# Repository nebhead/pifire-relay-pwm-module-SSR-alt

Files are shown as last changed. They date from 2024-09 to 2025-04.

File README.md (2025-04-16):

# PiFire Solid State Relay (SSR) Module PCB ALT (v1.0.0-alt) KiCad Files

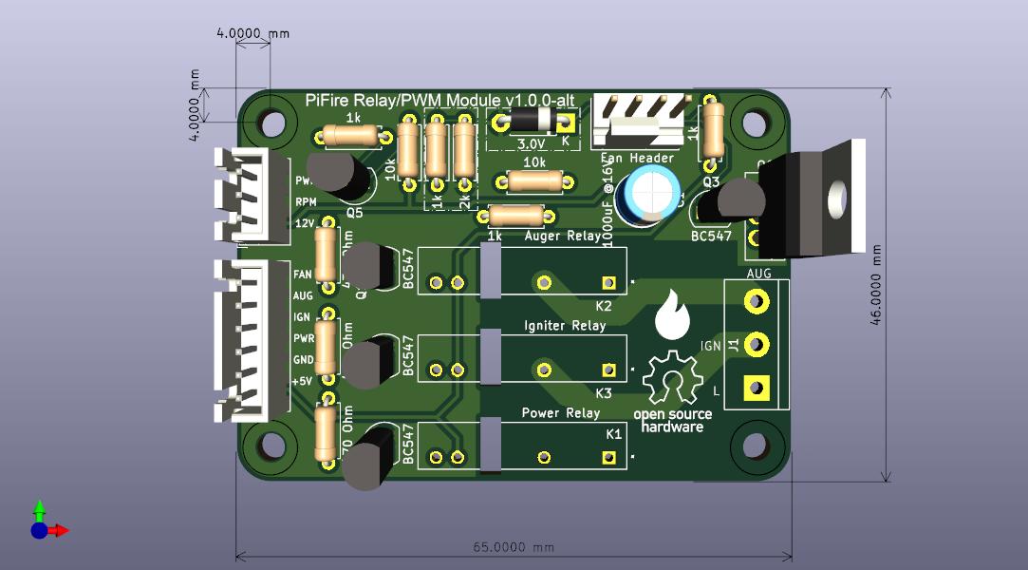
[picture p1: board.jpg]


## What is this? 

This PCB is designed to support SSR relays for controlling incoming Power(L) to the Igniter and Auger.  This board also has circuitry to support a 12V PWM fan.  This board uses compact solid state relays that are able to handle high power. This is an alternative to using an off the shelf relay module which simplifies the wiring and even allows you to use the OEM harness.

This version of the board was designed with help from user @labmonkeyrat on Discord. PCB mounted fuses have been removed, preferring inline fuses external to the board. The fan power is controlled from the high side (12V) instead of ground (original design).  

The design intent for this board was to make a DIY accessible PCB that can be more easily put together by the maker/enthusiast of almost any skill level.  Full size components are used in most cases and most (if not all) parts should be readily available to order online.  See the [Interactive BOM](#interactive-bom) for more details about the parts used and links to order.

### Important Notes

This PCB is intended to be used with the 4.0.x PCB design ([linked below](#links-to-the-pcbs-in-this-family-of-pifire-boards)) in conjunction with v1.8.x or later of the PiFire software.

The G3MB Relay footprints have been left out of this release because they were sourced from SnapMagic (for free), but are not licensed for re-distribution.  If you plan to edit this board, you may need to source those files from SnapMagic directly and add them to this project in the G3MB folder.

### What is PiFire? 

PiFire is a SBC based Pellet Smoker Controller.  More details can be found [here](https://nebhead.github.io/PiFire) or [at the GitHub repo](https://github.com/nebhead/pifire). 

## What's in this Repository?

### KiCad Project Files 
In this repository you will find the latest KiCad design files for the  PCB.  Simply load the project file (.kicad_pro) into the KiCad software and you should be able to edit as needed.  Or if you just want to get this board made, jump to the production section below.

### Interactive BOM

There is an interactive BOM located in the [/bom](bom/) folder which details the parts and provides some pin information as well.  Use this to gather the components you may need to build this board out and refer back to it for placement help.    

[BOM + Pin Info](https://nebhead.github.io/pifire-relay-pwm-module-SSR-alt)

_This is a standalone HTML file that was autogenerated by the excellent plugin for KiCad. See the plugin here: [https://github.com/openscopeproject/InteractiveHtmlBom](https://github.com/openscopeproject/InteractiveHtmlBom)_

### PDF of the Schematic

Preview the schematic in PDF format here: [Schematic](schematic.pdf)

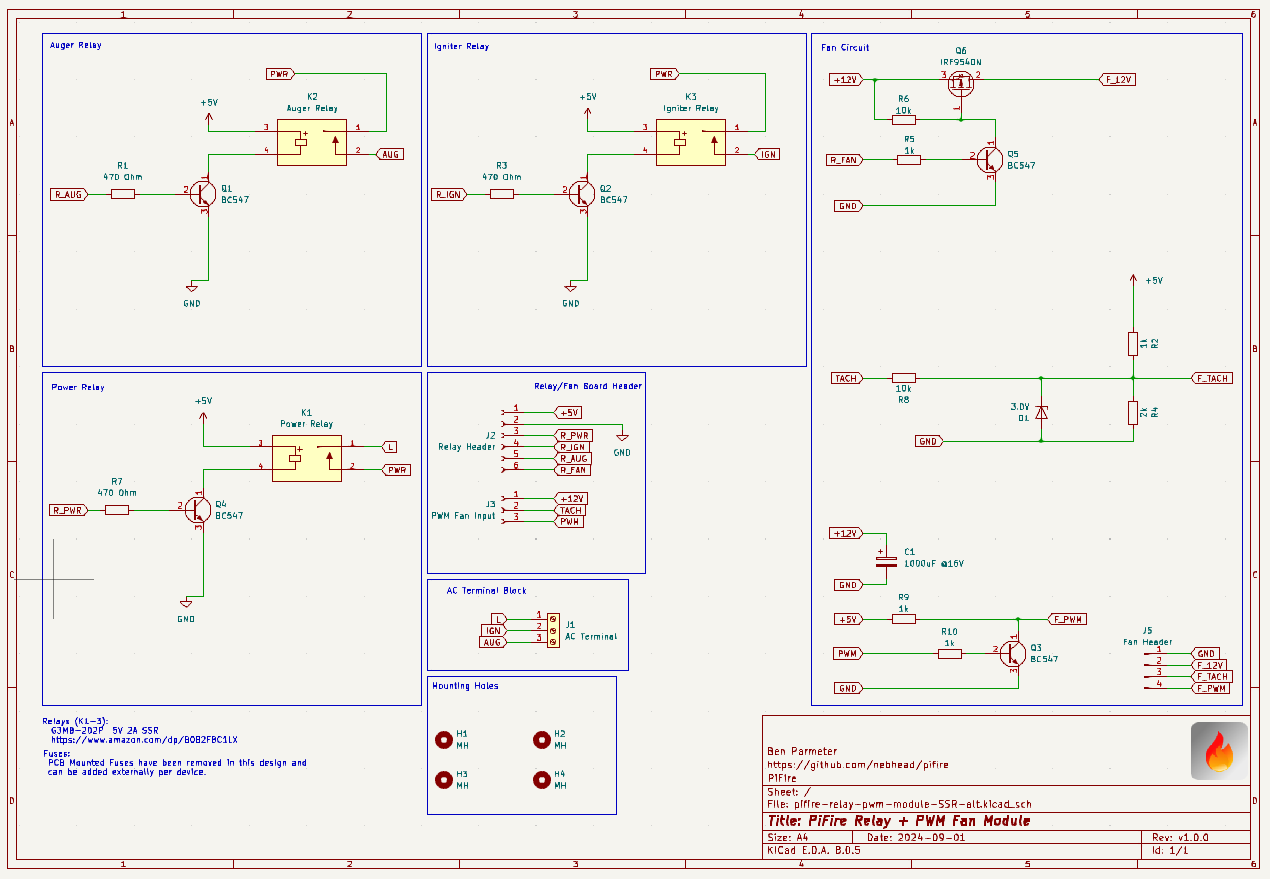
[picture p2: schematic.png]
Schematic PNG


### PWM Fan Pinout

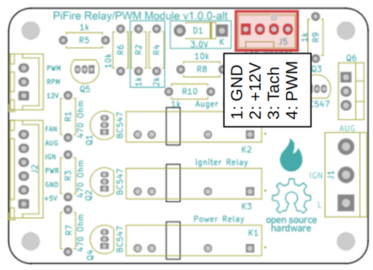
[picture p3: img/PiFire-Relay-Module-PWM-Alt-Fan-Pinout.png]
PWM Fan Pinout


The PWM fan pinout is using a standard 4-pin fan connector.  It's recommended to source the headers with retaining clip to ensure that the fan doesn't easily come unplugged.  JST headers can be used as well. 

### JLCPCB Production Files

If you wish to get these PCBs made by JLCPCB, the production files are provided in the `/production` folder.  For convenience, the file `production.zip` can simply be uploaded to JLCPCB to make it super easy to order boards.

Drop the zip file onto the order page, wait for it to upload then simply continue to order the board.  Optionally, select different board color, PCB quantity, surface finish, etc.  Most of the default settings should be sufficient. 

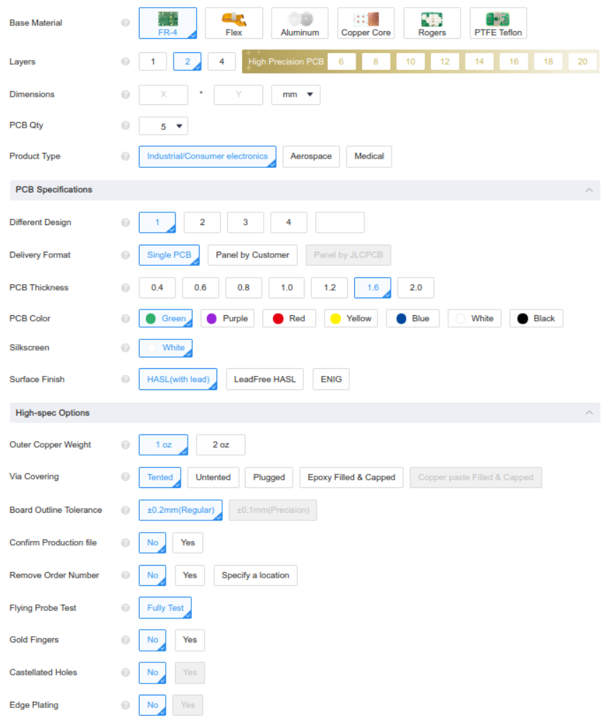
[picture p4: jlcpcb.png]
JLCPCB Order Page


### Links to the PCBs in this family of PiFire Boards

This PCB is part of a family of PCBs that can be used together to create  a full PiFire system.  Generally speaking you need the Main Module/Board, a Relay Control Board and a Probe Device board to have a basic PiFire system.  

**Main Module/Board** (required)
* [Main Board v4.0.x](https://github.com/nebhead/pifire-main-module-nopwr)

**Relay/Fan Control Boards** (choose one)
* [Mechanical Relay Module](https://github.com/nebhead/pifire-relay-module)
* [Solid State Relay Module](https://github.com/nebhead/pifire-relay-module-ssr)
* [Solid State Relay + PWM Fan Module](https://github.com/nebhead/pifire-relay-pwm-module-ssr) - Original Design
* [Solid State Relay + PWM Fan Module Alternate](https://github.com/nebhead/pifire-relay-pwm-module-ssr-alt) - Updated Design (Designed with help from @labmonkeyrat on Discord)

**Probe Device Board** (optional)
* [ADS Board](https://github.com/nebhead/pifire-ads-board) 

### 3D Printable Enclosures/Boxes 

With all of the 3D Prints for PiFire, a higher temperature filament such as PETG should be used.  PLA generally won't stand up to the temperatures that the components may be exposed to outdoors and near a hot smoker.  

#### Enclosure

Included here is an initial revision of the enclosure for this PCB.  The current models should be considered still in development and may have alignment challenges, etc. 

Except for the mounting wings, the majority of bolts to be used with this enclosure are M3. 

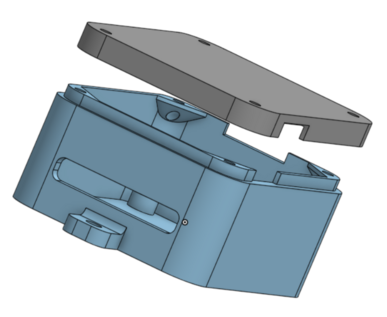
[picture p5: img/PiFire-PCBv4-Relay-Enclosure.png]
Enclosure


* STL: [Base](/printables/PiFire-v4-Relay-Base.stl)
* STL: [Lid](/printables/PiFire-v4-Relay-Lid.stl)
* OnShape: [Enclosure Original Models](https://cad.onshape.com/documents/03559f76f7adf190bf6f1259/w/7529cb0e4cd69db1a6a15202/e/07d5f9d46dc8f2b9e7dd655f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)

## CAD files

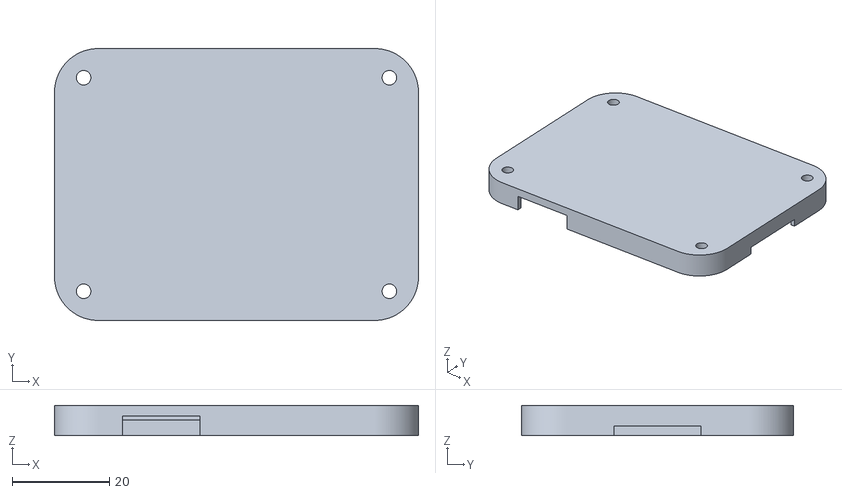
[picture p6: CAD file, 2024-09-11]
printables/PiFire-v4-Relay-Lid.stl
75.0 x 56.0 x 6.20

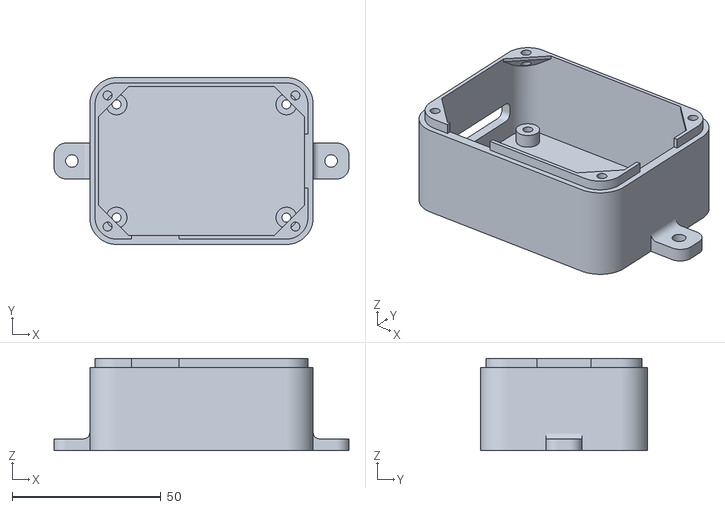
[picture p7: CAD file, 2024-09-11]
printables/PiFire-v4-Relay-Base.stl
99.0 x 56.0 x 31.0

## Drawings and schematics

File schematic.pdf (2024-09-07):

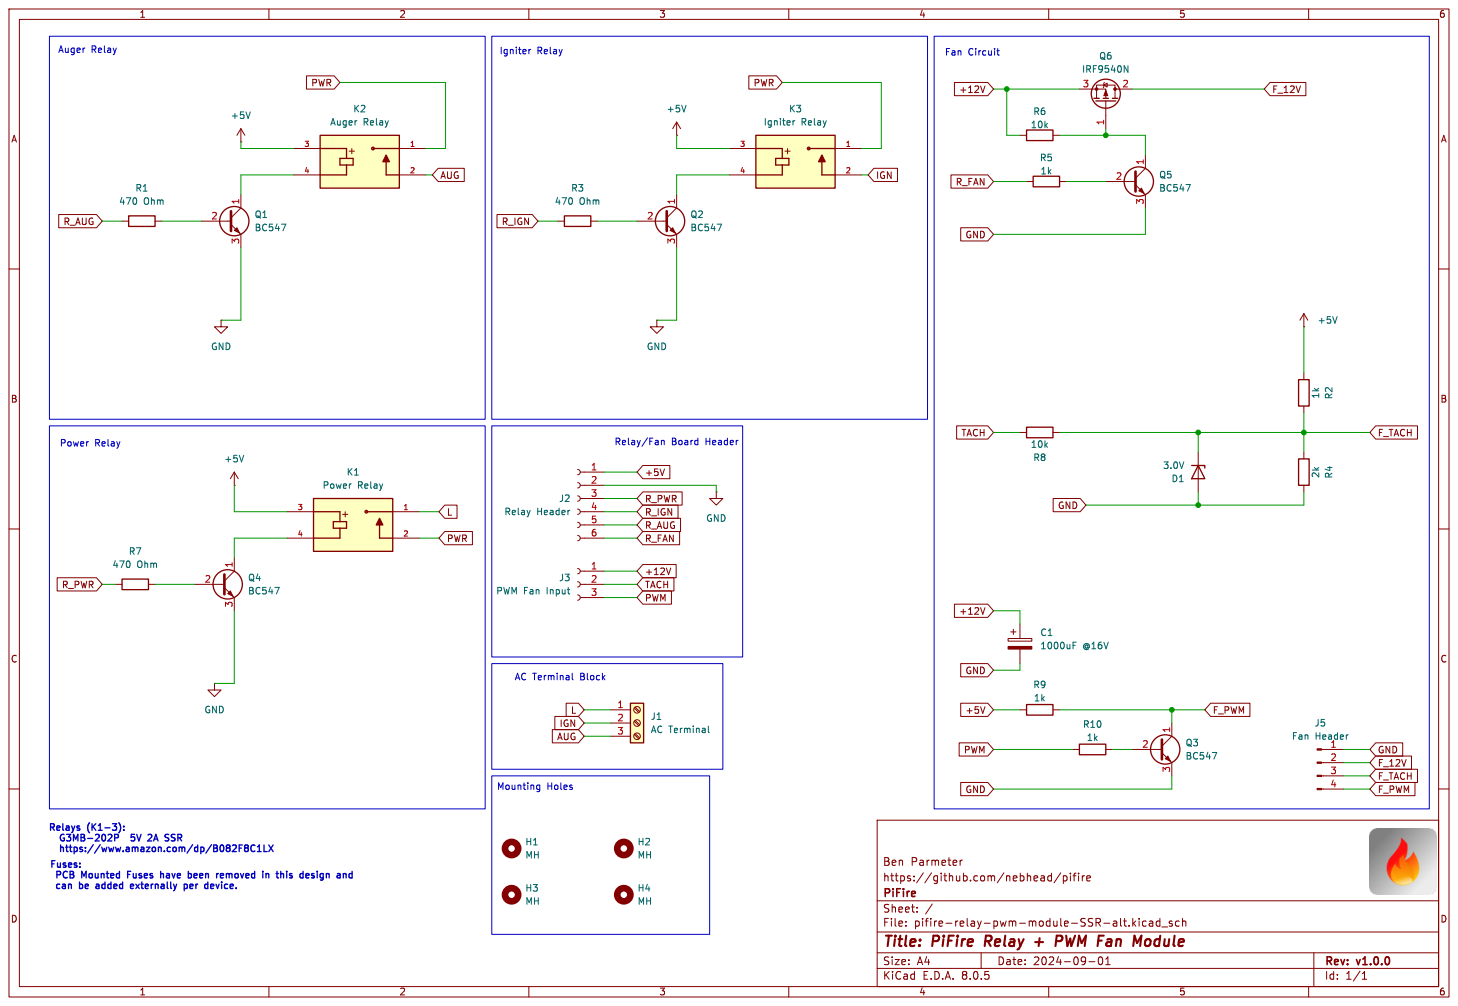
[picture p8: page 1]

https://www.amazon.com/dp/B082F8C1LX
Fuses: PCB Mounted Fuses have been removed in this design and

File: pifire-relay-pwm-module-SSR-alt.kicad_sch Sheet: / PiFire

Id: 1/1 Title: PiFire Relay + PWM Fan Module

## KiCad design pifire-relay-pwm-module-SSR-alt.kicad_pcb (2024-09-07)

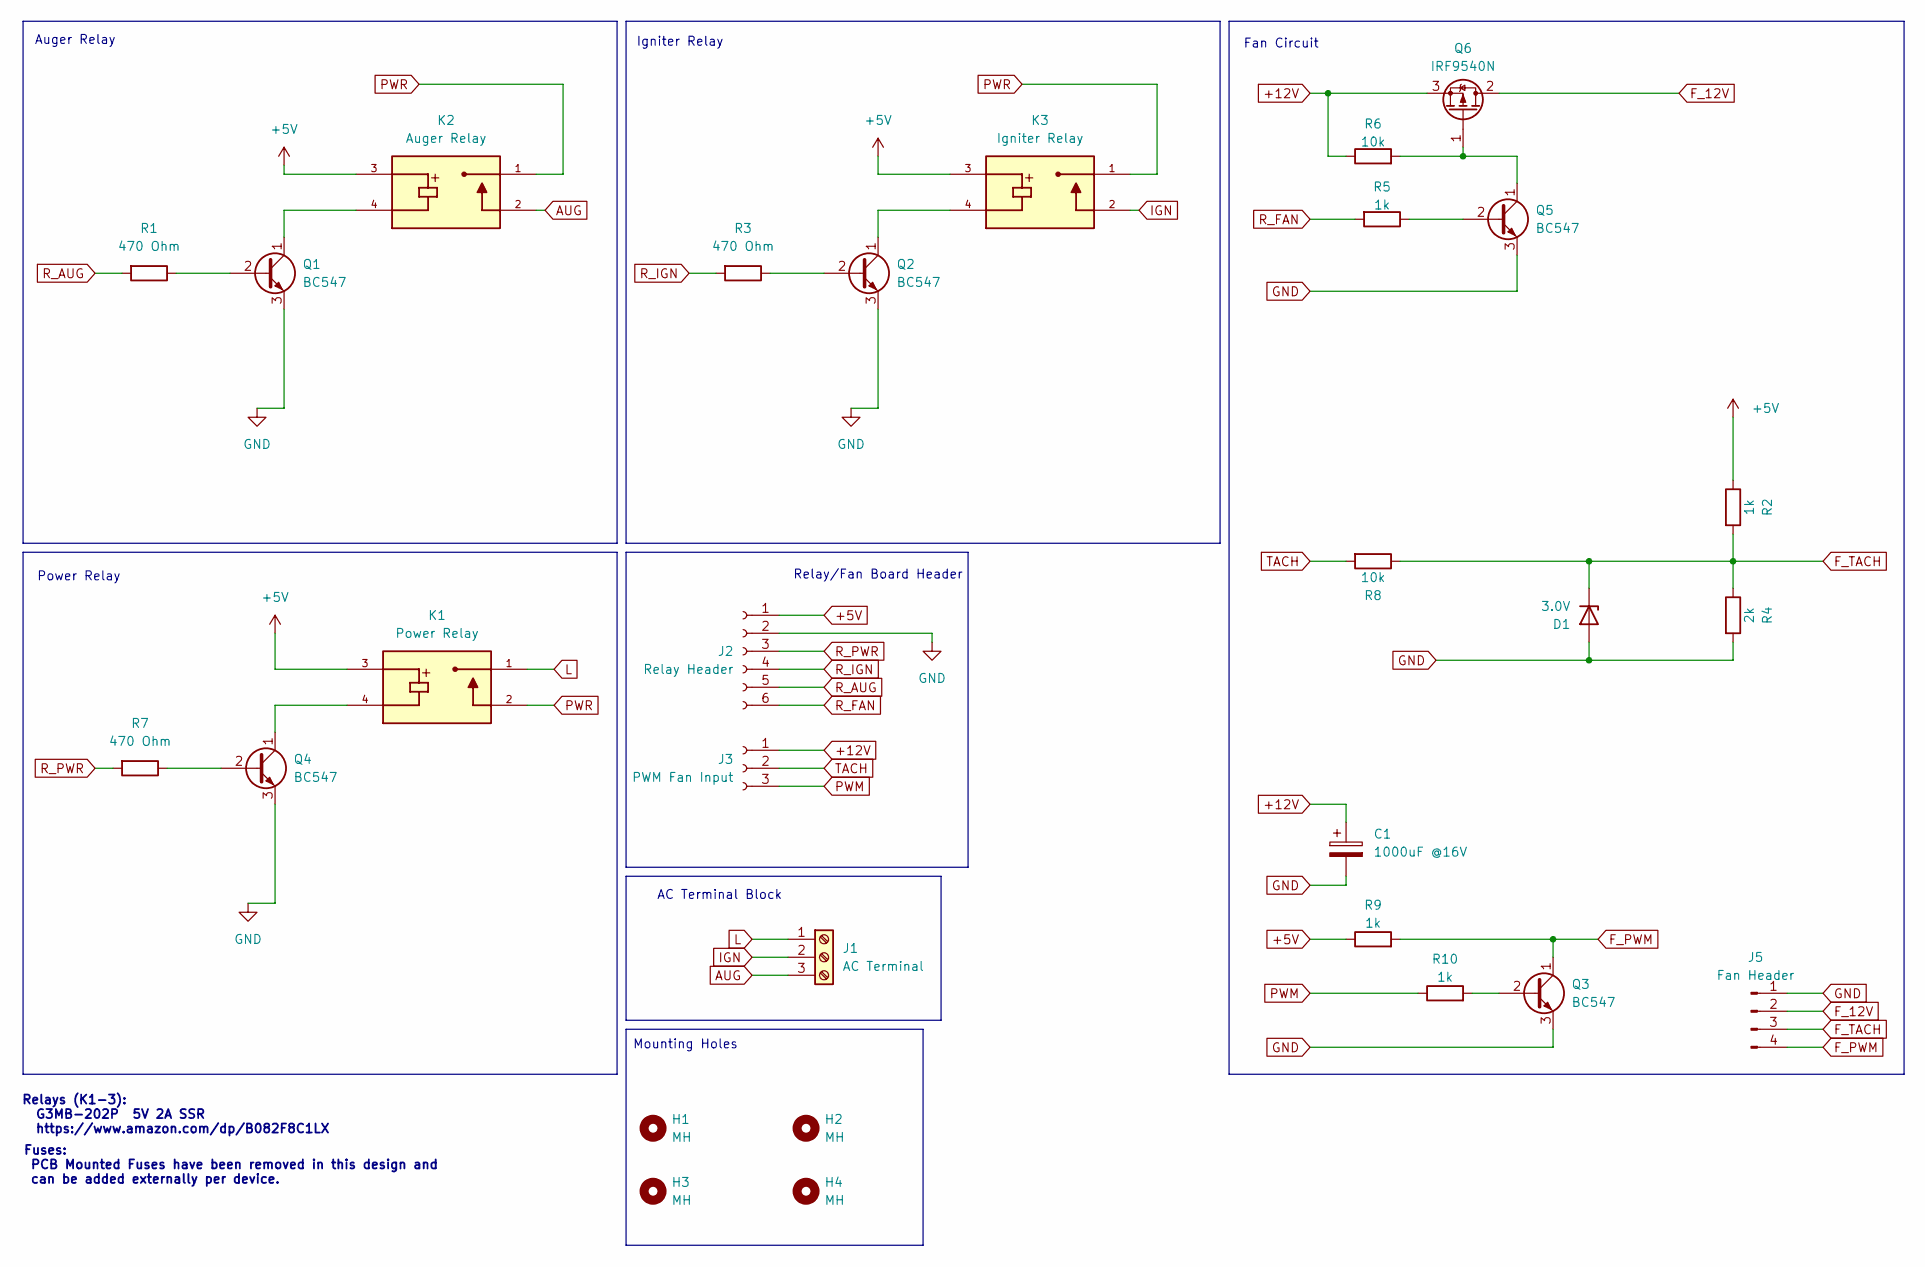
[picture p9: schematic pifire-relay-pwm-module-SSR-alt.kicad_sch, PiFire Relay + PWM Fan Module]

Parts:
C1: 1000uF @16V; CP_Radial_D6.3mm_P2.50mm
D1: 3.0V; D_DO-41_SOD81_P7.62mm_Horizontal
H1, H2, H3, H4: MH; MountingHole_3.2mm_M3
J1: AC Terminal; TerminalBlock_bornier-3_P5.08mm
J2: Relay Header; JST_XH_B6B-XH-A_1x06_P2.50mm_Vertical
J3: PWM Fan Input; JST_XH_B3B-XH-A_1x03_P2.50mm_Vertical
J5: Fan Header; FanPinHeader_1x04_P2.54mm_Vertical
K1: Power Relay; RELAY_G3MB-202PDC5; PARTREV J091-E1-1A
K2: Auger Relay; RELAY_G3MB-202PDC5; PARTREV J091-E1-1A
K3: Igniter Relay; RELAY_G3MB-202PDC5; PARTREV J091-E1-1A
Q1, Q2, Q3, Q4, Q5: BC547; TO-92L_Inline
Q6: IRF9540N; TO-220-3_Vertical
R1, R3, R7: 470 Ohm; R_Axial_DIN0207_L6.3mm_D2.5mm_P7.62mm_Horizontal
R2, R5, R9, R10: 1k; R_Axial_DIN0207_L6.3mm_D2.5mm_P7.62mm_Horizontal
R4: 2k; R_Axial_DIN0207_L6.3mm_D2.5mm_P7.62mm_Horizontal
R6, R8: 10k; R_Axial_DIN0207_L6.3mm_D2.5mm_P7.62mm_Horizontal

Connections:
+5V: J2.1, K1.3, K2.3, K3.3, R2.1, R9.1
+12V: C1.1, J3.1, Q6.3 (S), R6.1
AUG: J1.3, K2.2
F_12V: J5.2, Q6.2 (D)
F_PWM: J5.4, Q3.1 (C), R9.2
F_TACH: D1.1 (K), J5.3, R2.2, R4.1, R8.1
GND: C1.2, D1.2 (A), J2.2, J5.1, Q1.3 (E), Q2.3 (E), Q3.3 (E), Q4.3 (E), Q5.3 (E), R4.2
IGN: J1.2, K3.2
L: J1.1, K1.1
unnamed: Q1.2 (B), R1.1
unnamed: K2.4, Q1.1 (C)
unnamed: Q2.2 (B), R3.1
unnamed: K3.4, Q2.1 (C)
unnamed: Q3.2 (B), R10.2
unnamed: Q4.2 (B), R7.1
unnamed: K1.4, Q4.1 (C)
unnamed: Q5.2 (B), R5.1
unnamed: Q5.1 (C), Q6.1 (G), R6.2
PWM: J3.3, R10.1
PWR: K1.2, K2.1, K3.1
R_AUG: J2.5, R1.2
R_FAN: J2.6, R5.2
R_IGN: J2.4, R3.2
R_PWR: J2.3, R7.2
TACH: J3.2, R8.2

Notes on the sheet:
Fan Circuit
Power Relay
Fuses: PCB Mounted Fuses have been removed in this design and can be added externally per device.
AC Terminal Block
Auger Relay
Relay/Fan Board Header
Relays (K1-3): G3MB-202P 5V 2A SSR https://www.amazon.com/dp/B082F8C1LX
Mounting Holes
Igniter Relay

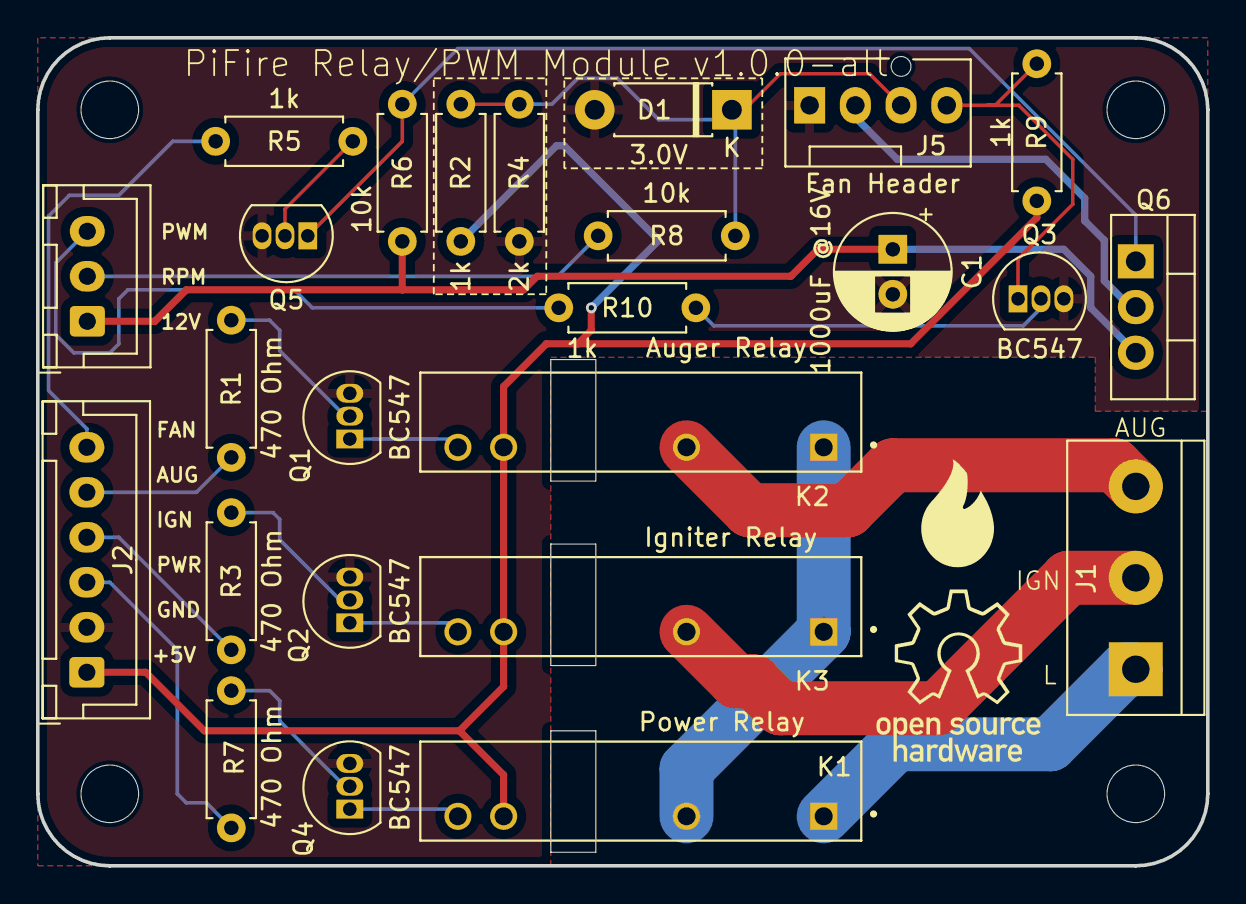
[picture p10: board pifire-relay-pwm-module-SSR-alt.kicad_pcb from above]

Board: 2 copper layers, 65.0 x 46.0 mm, 29 parts (0 on the bottom side), 25 nets.

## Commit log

2024-09-07 Adding Project Files
    [pifire-relay-pwm-module-SSR-alt-B_Cu.gbl, pifire-relay-pwm-module-SSR-alt-B_Mask.gbs, pifire-relay-pwm-module-SSR-alt-B_Paste.gbp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]
2024-09-07 Updated Production Files with Latest
    [pifire-relay-pwm-module-SSR-alt-B_Cu.gbl, pifire-relay-pwm-module-SSR-alt-B_Mask.gbs, pifire-relay-pwm-module-SSR-alt-B_Paste.gbp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]
2024-09-07 Add board image
2024-09-11 Added 3D Printables
    [PiFire-v4-Relay-Base.stl, PiFire-v4-Relay-Lid.stl]
2025-04-16 Updated with PWM Fan Pinout
